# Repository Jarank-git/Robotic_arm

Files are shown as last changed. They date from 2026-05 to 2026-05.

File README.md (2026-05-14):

# Robotic Arm: Record/Playback & Hand Control

A robotic arm with four axes that is programmed using the Arduino Nano board and a shield. It offers four modes of control, namely, direct control using potentiometers, recording and playing back positions, and hand gestures using computer vision, all available and switchable over serial communication in real time.



## How It Works

The robotic arm consists of four joints that are powered by MG90S and SG90 servo motors. Four potentiometers are used as the main source of input control, with one for each joint. When turning a knob manually, it rotates its associated joint in real time. The Arduino Nano scans each potentiometer, converts the value to a corresponding pulse width in microseconds for the servo motor, and sends commands to the four servos in a timely manner. In addition to direct control, there are three other modes available, such as record, play, and gesture, all of which can be switched through serial communication.

| Command | Mode | Description |
|---|---|---|
| `0` | Normal | Potentiometers control servos in real time |
| `1` | Record | Position the arm and send `r` to save each step (up to 100) |
| `2` | Playback | Smooth looping replay of recorded steps |
| `3` | Gesture | Python takes over servo control via webcam |
| `h` | Help | Prints command menu to serial monitor |

## Firmware

Smooth motion of the arm without jitters involved many factors, among them averaging of multiple sensor values, careful handling of microseconds of signal for each joint's servos.

Averaging. The readings of each potentiometer are averaged after 30 sequential readings, 100µs apart from each other. Otherwise, consecutive readings of analog signals will be affected by noise caused by capacitive effects, which manifest themselves in a permanent jittery behavior of the servos. Averaging the results over 30 times eliminates such artifacts.

Microsecond control. The servos are controlled not by write(), but by writeMicroseconds(). The former only offers 0-180 positions with an integer number between them. Using writeMicroseconds() allows for controlling the servo in a wide range of about 600-2400µs which is enough for smooth interpolation.

Timed polling loop. Reading the sensors as quickly as possible would produce jittery behavior as well as out-of-synchronicity of the joints. The firmware does its work at a predefined frequency of 25ms. Four potentiometers are read and all four servos' positions are updated in one sequence of actions: readPot(), mapping(), then move_servo(). Thus, the joints are always synchronized.

Array-based design. The values of ADC measurements of potentiometers are stored in sensVal[4]. Then, each of these numbers is converted to microseconds with map() function and stored in ist[4]. Then, move_servo() uses the numbers in this array to control the servo positions. In record mode, current ist[] array is copied to four different arrays named joint0-joint3 of 100 elements length.

Potentiometer calibration. The map() function is applied to convert sensVal[i] to ist[i] by calling map(sensVal[i], 0, 650, 600, 2400). This map uses 650 as an upper limit while 1023 is the actual maximum value. After measuring the actual rotation angle of the potentiometer, I found that only a limited rotation gives max ADC value. Therefore, the maximum value for potentiometer rotation was actually 650, and using it as the upper boundary allows for recording a full rotation without any problems.

Ease-in-out playback. When playing back the recorded data, the transitions are not abrupt. A smooth movement of the arm happens due to interpolation and cosine easing algorithm which splits each transition into 50 steps, making the whole transition take about 800ms. The cosine function generates a natural movement pattern, starting slow as the joint accelerates, reaching peak speed through the middle, then decelerating to a stop at the target position.

## Gesture Control

The gesture control script uses MediaPipe Hands to track a hand through a webcam feed and maps the number of extended fingers to servo axes on the arm. MediaPipe returns 21 landmarks per hand, one for each joint and fingertip. To determine whether a finger is extended, the script compares the y-coordinate of the fingertip landmark to the y-coordinate of the knuckle two joints down. Since y increases downward in image coordinates, a fingertip with a lower y value than its knuckle means the finger is pointing up and therefore extended.

The finger count maps directly to which servo moves: 1 finger drives servo 1, 2 fingers servo 2, and so on. Each servo has a direction variable that starts positive, incrementing the position by a fixed step each frame. When the position hits the 2400µs ceiling or 600µs floor, the direction flips and the servo starts moving back. This gives continuous bouncing motion as long as fingers are held up, which makes it intuitive to control. The number of fingers held up determines which joint is active.

The script connects to the Nano on COM3 at 9600 baud, sends a 3 to switch it into gesture mode, and then streams S s1 s2 s3 s4 commands every frame. The Nano parses each incoming S command and writes the four values directly to the servos.

Dependencies: pyserial, opencv-python, mediapipe

## Assembly

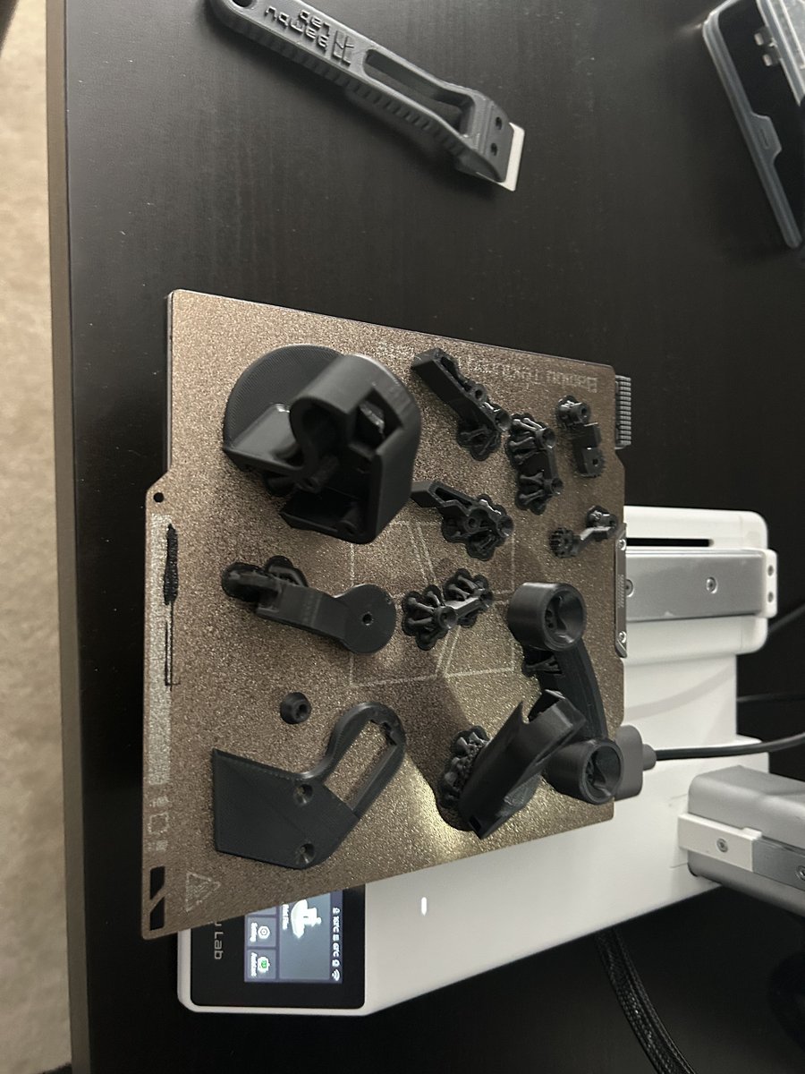
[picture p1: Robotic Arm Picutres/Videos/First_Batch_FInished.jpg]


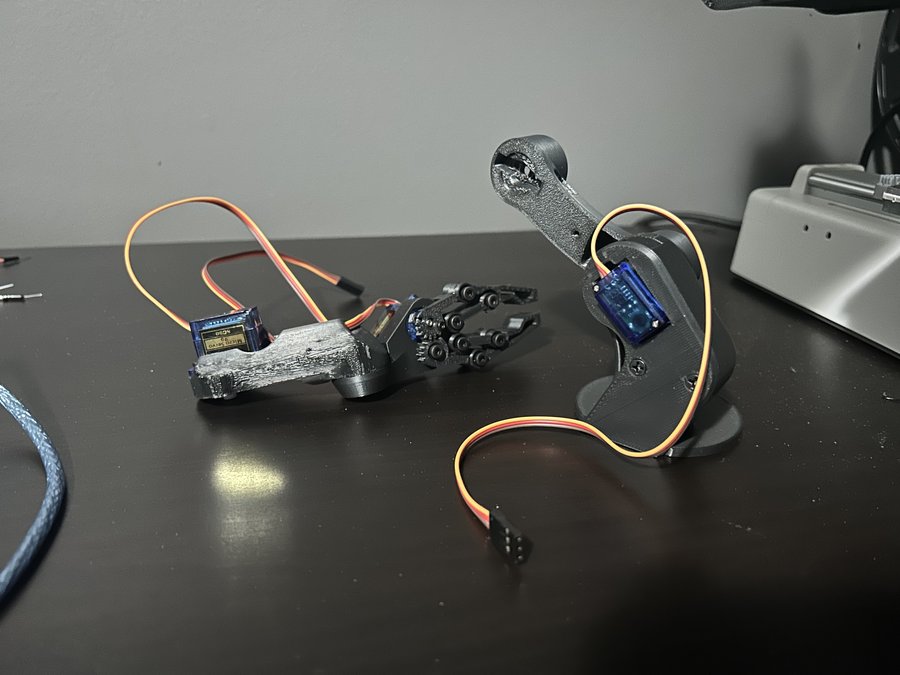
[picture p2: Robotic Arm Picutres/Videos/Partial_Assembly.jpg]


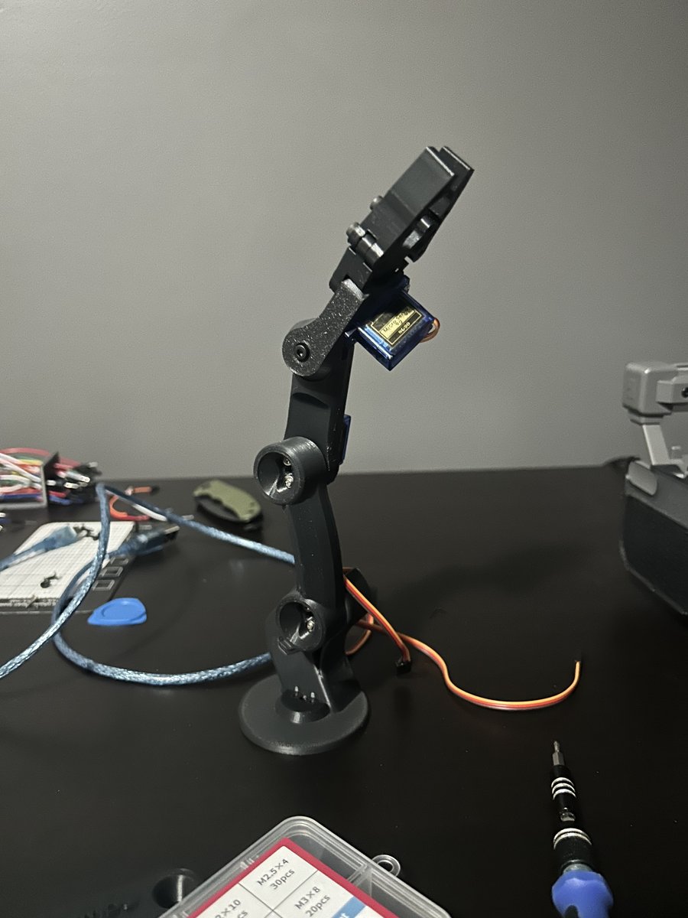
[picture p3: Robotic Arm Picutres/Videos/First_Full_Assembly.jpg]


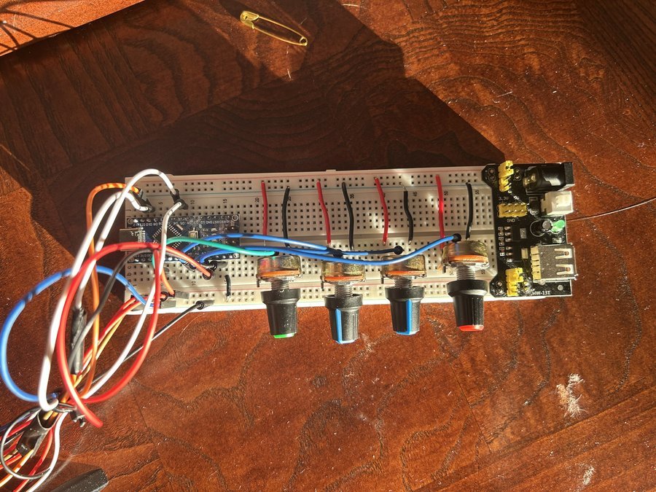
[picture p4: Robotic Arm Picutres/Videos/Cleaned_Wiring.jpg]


All the parts were made using PLA through 3D printing. However, there were a few modifications made before the parts were finalized. Initially, the prints came out perfect, and assembly progressed well until it was time to test the claw. The first problem was with the claw. The screw hole position in the original part file was inaccurate, resulting in improper interaction between the gears attached to the fingers of the claw. This led to a situation where only one claw out of the two was correctly closing, the other was not recieving power through the gears. To correct this problem, I uploaded the part file to Autodesk Fusion and then measured the distance from the screw hole to its required position based on the gear geometry. This information was used to relocate the hole, and then it was reprinted successfully, and the mechanism worked in the desired way. The next problem encountered was with the connector arm. The connector arm is a component that connects the claw to the main arm through a channel meant for an M3 nut that screws into the claw mechanism. The channel was small and not able to hold the nut. This problem was corrected by opening up the channel in Autodesk Fusion and then reprinting the part successfully. Both modified STEP files are in the CAD folder with full credit to the original designer.

## PCB & Schematics

The first prototype of the build made use of a breadboard to link up the Nano, potentiometers, and servo signal lines. It did work, although it was untidy and prone to failure; wires would move out of place and connections would come loose when the robot moved. In order to make things cleaner and more efficient, I came up with a design for my own PCB shield, done using Altium Designer. This allows all the components to fit onto one PCB, which is placed on top of the Nano. The Altium source files are included in the PCB + Schematic folder.

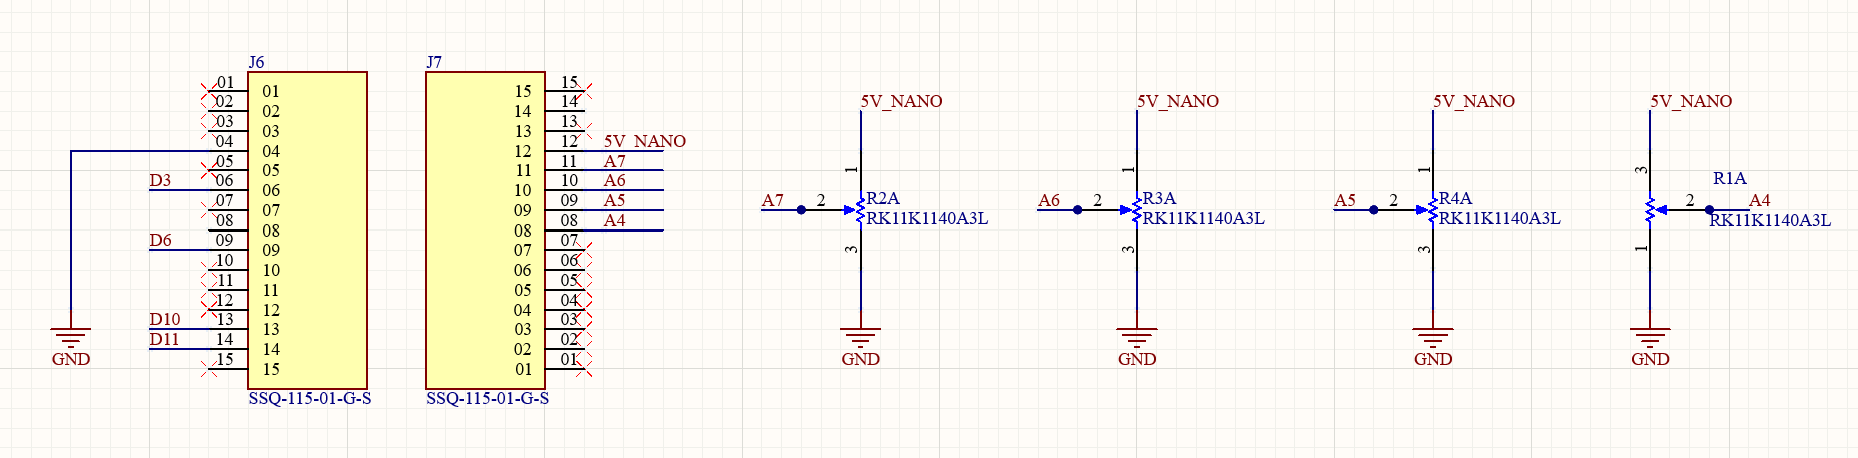
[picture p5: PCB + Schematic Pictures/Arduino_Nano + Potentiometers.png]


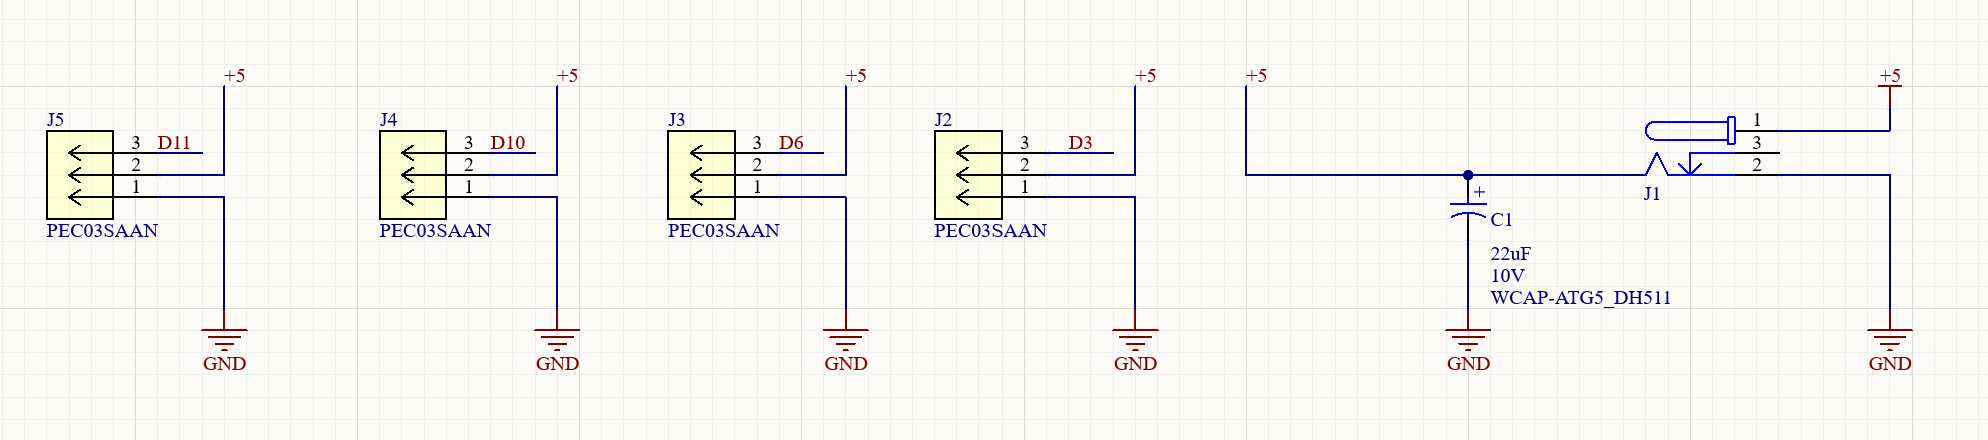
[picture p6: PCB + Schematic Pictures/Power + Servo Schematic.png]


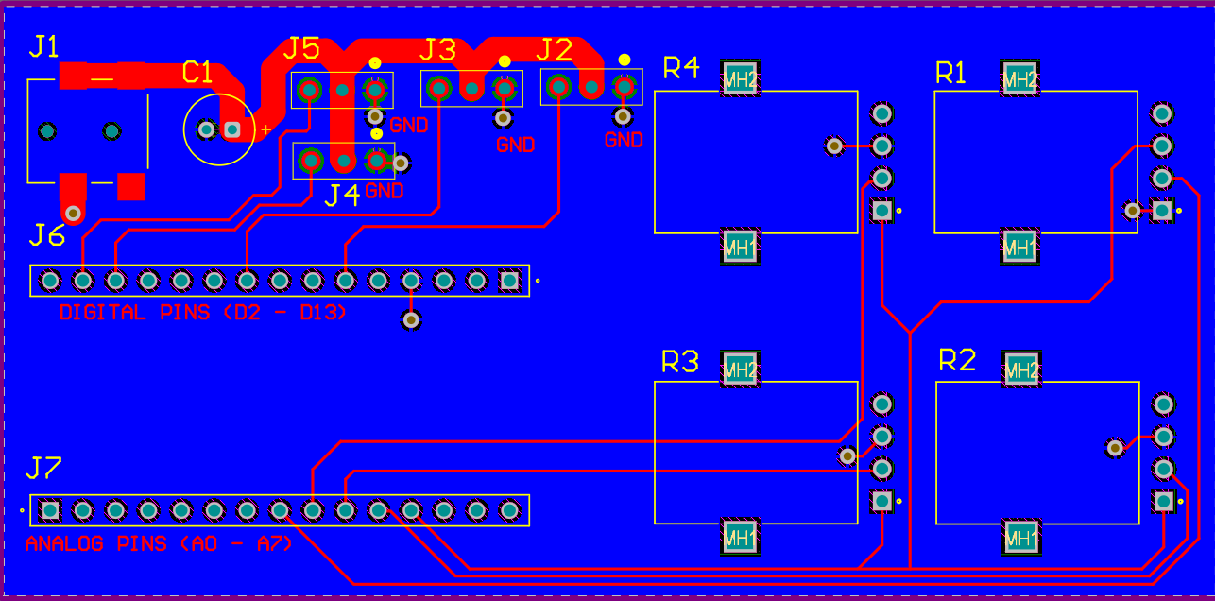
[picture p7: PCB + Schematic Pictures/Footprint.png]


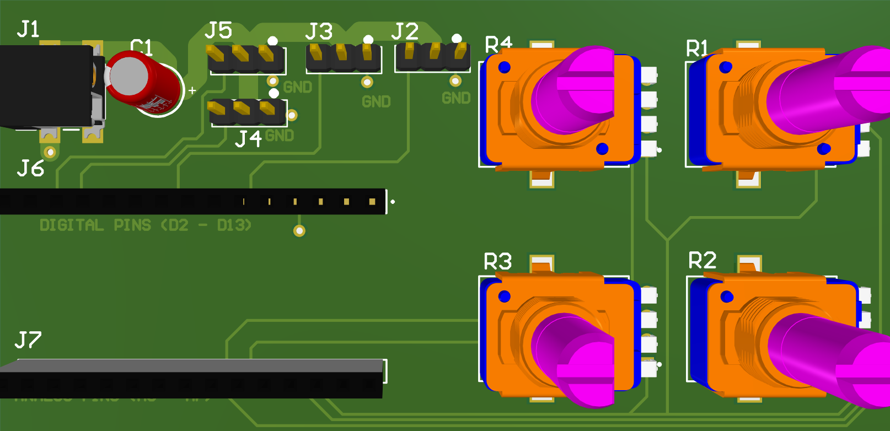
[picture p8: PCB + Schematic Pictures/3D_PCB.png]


## Hardware

| Component | Details |
|---|---|
| Microcontroller | Arduino Nano (ATmega328P) |
| Servos | 4× MG90S / SG90 |
| Potentiometers | 4× 10kΩ |
| Wiring | Jumper wires |
| PCB | Custom shield designed in Altium Designer |
| 3D Printed Parts | PLA |
| Framework | PlatformIO |

## Demo Videos

- Gesture Control: https://youtu.be/HV5-AcP3Ts8
- Record / Playback: https://youtu.be/INzKYXssj1g
- Manual Control: https://youtu.be/m88PAH4PIvc

## Build & Flash

Requires [PlatformIO](https://platformio.org/). With the Nano on COM3:

```bash
pio run --target upload
pio device monitor --baud 9600
```

Send h in the serial monitor for the full command reference.

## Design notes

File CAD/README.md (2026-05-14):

# CAD Files

## Credits

The original robotic arm models were designed by **FABRI CREATOR** — all credit for the base design goes to them.

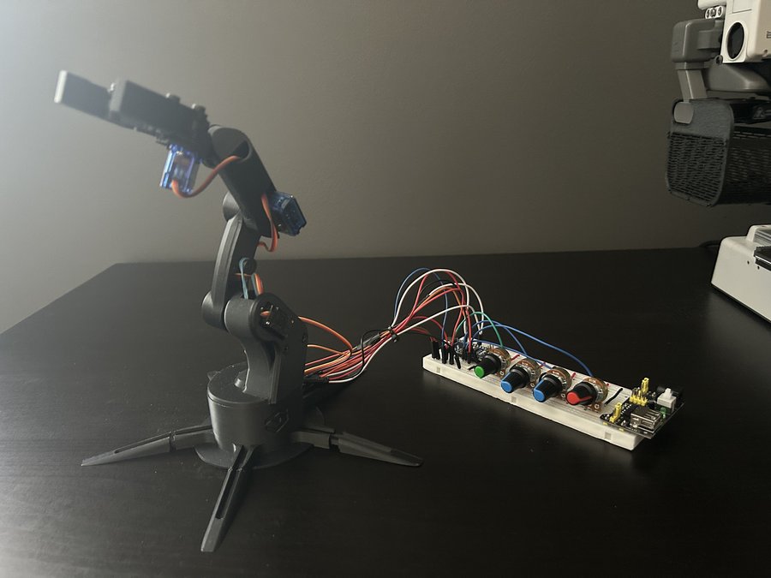
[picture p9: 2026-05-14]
Robotic Arm Picutres/Videos/Final_Product.jpg

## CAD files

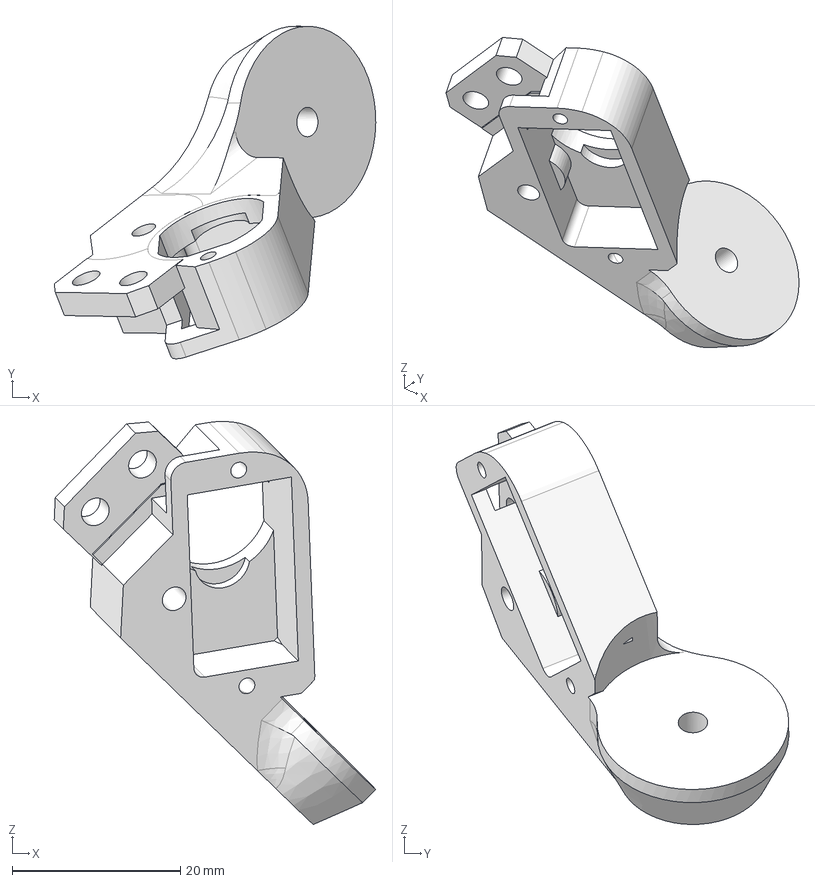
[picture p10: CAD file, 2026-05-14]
CAD/Modified+Claw+Arm.stp
38.3 x 39.6 x 48.0 mm
SG90 - Micro Servo 9g - Tower Pro v2
SG90 - Micro Servo 9g - Tower Pro.3 (1) x 2
SG90 - Micro Servo 9g - Tower Pro.5 (1) x 4
SG90 - Micro Servo 9g - Tower Pro.6 (1) x 2
Engranaje1
Engranaje2
Barra2
Garra1
Barra1
Garra2
Eje Garra2 (1)
Base de la Garra x 2
SG90 - Micro Servo 9g - Tower Pro.1 (1)
Servo sg90 (1)
Antebrazo
Brazo
Base (2) x 2
Eje Central (1)
Potentiometer (1)
Engranaje1 (1)
Engranaje2 (1)
Garra1 (1)
Barra2 (1)
Barra1 (1)
Garra2 (1)
Base de la Garra (1)
SG90 SERVOMOTOR x 3
Potentiometer (1) v1 (5)
Potentiometer (1) v1 (6)
Potentiometer (1) v1 (7)
Potentiometer (1) v1 (8)
Antebrazo (1)
Brazo (1)
Base (2) (1) x 2
Tapa Eje
Tubito
Eje Central (1) (1)
perilla v12
perilla v12 (1)
perilla v12 (2)
perilla v12 (3)
Base del brazo y circuito
Pata (1)
Pata (4)
Pata (3)
Pata (2)
Tapa para potenciometros solos(1)
Caja de solo potenciómetros(1)
Pata(5)

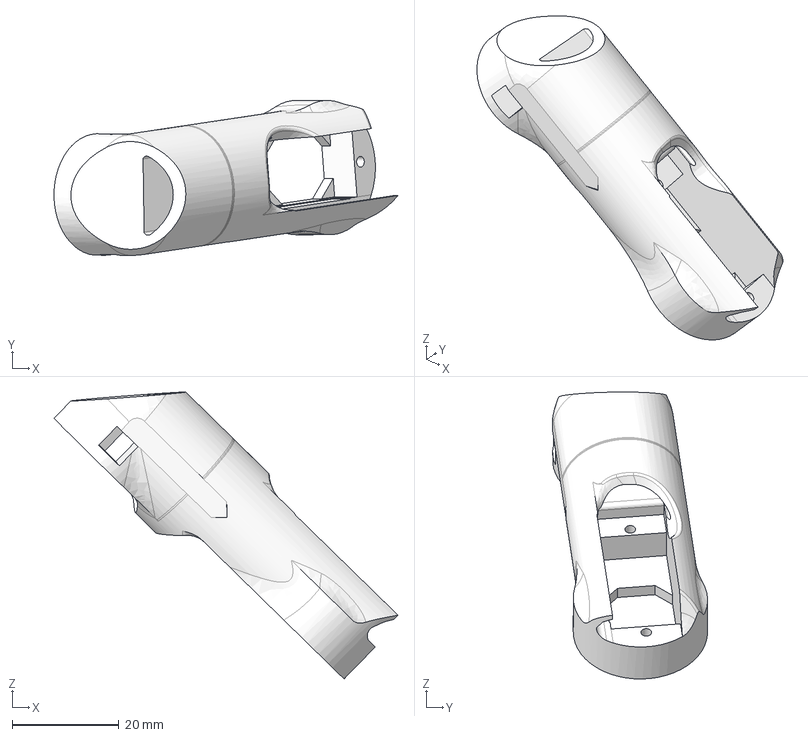
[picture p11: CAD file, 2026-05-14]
CAD/Modified+Connector+Arm.stp
64.5 x 29.1 x 53.8 mm
SG90 - Micro Servo 9g - Tower Pro v2
SG90 - Micro Servo 9g - Tower Pro.3 (1) x 2
SG90 - Micro Servo 9g - Tower Pro.5 (1) x 4
SG90 - Micro Servo 9g - Tower Pro.6 (1) x 2
Engranaje1
Engranaje2
Barra2
Garra1
Barra1
Garra2
Eje Garra2 (1)
Base de la Garra x 2
SG90 - Micro Servo 9g - Tower Pro.1 (1)
Servo sg90 (1)
Antebrazo
Brazo
Base (2) x 2
Eje Central (1)
Potentiometer (1)
Engranaje1 (1)
Engranaje2 (1)
Garra1 (1)
Barra2 (1)
Barra1 (1)
Garra2 (1)
Base de la Garra (1)
SG90 SERVOMOTOR x 3
Potentiometer (1) v1 (5)
Potentiometer (1) v1 (6)
Potentiometer (1) v1 (7)
Potentiometer (1) v1 (8)
Antebrazo (1)
Brazo (1)
Base (2) (1) x 2
Tapa Eje
Tubito
Eje Central (1) (1)
perilla v12
perilla v12 (1)
perilla v12 (2)
perilla v12 (3)
Base del brazo y circuito
Pata (1)
Pata (4)
Pata (3)
Pata (2)
Tapa para potenciometros solos(1)
Caja de solo potenciómetros(1)
Pata(5)

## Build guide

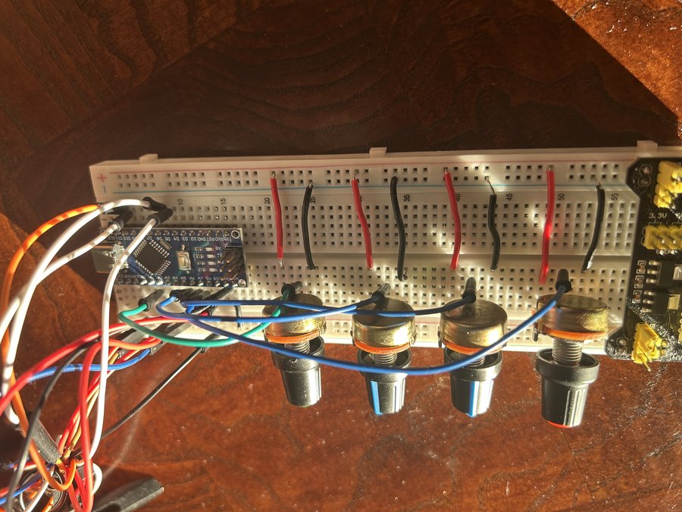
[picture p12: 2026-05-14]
Robotic Arm Picutres/Videos/Wiring.jpg

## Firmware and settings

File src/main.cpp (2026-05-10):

#include <Arduino.h>
#include <Servo.h>

Servo servo1;
Servo servo2;
Servo servo3;
Servo servo4;
int joint0[100];
int joint1[100];
int joint2[100];
int joint3[100];
int mode(0);
int stepCount(0);
int currentStep(0);
int sensVal[4];
float ist[4];
unsigned long previous_time(0);
unsigned long lastRecord(0);
int lastMode(-1);
const int stepDuration = 800; // ms per step transition during playback

// ease-in-out curve slow start, fast middle, slow end for natural motion, using a fcn (cos) to model the behaviour
float easeInOut(float t) {
    return -(cos(PI * t) - 1.0f) / 2.0f;
}

//fcn to smoothly move servos from one recorded position to the next over duration_ms
void smoothMove(int f0, int t0, int f1, int t1, int f2, int t2, int f3, int t3, int duration_ms) {
    const int steps = 50;
    int stepDelay = duration_ms / steps;
    for (int i = 0; i <= steps; i++) {
        //check for mode change midmove so user can interrupt
        if (Serial.available() > 0) break;
        float ease = easeInOut((float)i / steps);
        servo1.writeMicroseconds(f0 + ease * (t0 - f0));
        servo2.writeMicroseconds(f1 + ease * (t1 - f1));
        servo3.writeMicroseconds(f2 + ease * (t2 - f2));
        servo4.writeMicroseconds(f3 + ease * (t3 - f3));
        delay(stepDelay);
    }
}

//function to average the analogRead from each potentiometer to reduce noise, thus reducing jittering
unsigned int averageFcn(int pin) {
    unsigned int count(0);
    for(unsigned int i(0); i < 30; i++){
        count += analogRead(pin);
        delayMicroseconds(100);
    }
    count /= 30;
    return count;
}

void readPot() {
    sensVal[0] = averageFcn(A7);
    sensVal[1] = averageFcn(A6);
    sensVal[2] = averageFcn(A5);
    sensVal[3] = averageFcn(A1);
}


//mapping the manual potentiometer values, 0 - 650 calibrated for my setup, to 600 - 2400 for microsecond movements
void mapping() {
    ist[0] = map(sensVal[0], 0, 650, 600, 2400);
    ist[1] = map(sensVal[1], 0, 650, 600, 2400);
    ist[2] = map(sensVal[2], 0, 650, 600, 2400);
    ist[3] = map(sensVal[3], 0, 650, 600, 2400);
}

//function to merge all servo movements into 1 fcn
void move_servo() {
    servo1.writeMicroseconds(ist[0]);
    servo2.writeMicroseconds(ist[1]);
    servo3.writeMicroseconds(ist[2]);
    servo4.writeMicroseconds(ist[3]);
}

// fcn that handles recording each servo motor's movement to the respective array
void recordStep() {
    if (stepCount < 100) {
        // use the ist[] values already updated by the loop — no need to re-read pots
        joint0[stepCount] = ist[0];
        joint1[stepCount] = ist[1];
        joint2[stepCount] = ist[2];
        joint3[stepCount] = ist[3];
        stepCount++;

        Serial.print("Step ");
        Serial.print(stepCount);
        Serial.println(" recorded. Send 'r' for next step, '2' to play back.");
    } else {
        Serial.println("Memory full (100 steps). Send '2' to play back.");
    }
}

// fcn to handle the playback of the values stored in the array from the recordStep fcn
void playBack() {
    if (stepCount == 0) {
        Serial.println("No steps recorded. Record some first (send '1', then 'r').");
        mode = 0;
        return;
    }

    //on first step, snap directly to starting position then begin smooth transitions
    if (currentStep == 0) {
        servo1.writeMicroseconds(joint0[0]);
        servo2.writeMicroseconds(joint1[0]);
        servo3.writeMicroseconds(joint2[0]);
        servo4.writeMicroseconds(joint3[0]);
        currentStep = 1;
        return;
    }

    Serial.print("Playing step ");
    Serial.print(currentStep + 1);
    Serial.print(" / ");
    Serial.println(stepCount);

    smoothMove(
        joint0[currentStep - 1], joint0[currentStep],
        joint1[currentStep - 1], joint1[currentStep],
        joint2[currentStep - 1], joint2[currentStep],
        joint3[currentStep - 1], joint3[currentStep],
        stepDuration
    );

    currentStep++;
    if (currentStep >= stepCount) {
        currentStep = 0;
        Serial.println("Loop complete. Repeating... Send '0' to stop.");
    }
}

//prints the command menu to the serial monitor
void printHelp() {
    Serial.println("--- Commands ---");
    Serial.println("  0  : Normal mode (potentiometer control)");
    Serial.println("  1  : Record mode (position arm, send 'r' to save each step)");
    Serial.println("  2  : Playback mode (smooth replay of recorded steps)");
    Serial.println("  3  : Gesture mode (python controls servos)");
    Serial.println("  r  : Record current position (record mode only)");
    Serial.println("  h  : Show this help");
    Serial.println("----------------");
}


//reads and processes all incoming serial commands (mode switches, record trigger, gesture S commands)
void handleButtons() {
    while (Serial.available() > 0) {
        char cmd = Serial.read();
        if (cmd == '\r' || cmd == '\n') continue;

        if (cmd == '0') { mode = 0; }
        else if (cmd == '1') { mode = 1; stepCount = 0; }
        else if (cmd == '2') { mode = 2; currentStep = 0; }
        else if (cmd == '3') { mode = 3; }
        else if (cmd == 'S') {
            char buf[24];
            int len = Serial.readBytesUntil('\n', buf, sizeof(buf) - 1);
            if (mode == 3) {
                buf[len] = '\0';
                int s1, s2, s3, s4;
                if (sscanf(buf, "%d %d %d %d", &s1, &s2, &s3, &s4) == 4) {
                    servo1.writeMicroseconds(s1);
                    servo2.writeMicroseconds(s2);
                    servo3.writeMicroseconds(s3);
                    servo4.writeMicroseconds(s4);
                }
            }
        }
        else if (cmd == 'r' && mode == 1 && millis() - lastRecord > 300) {
            readPot();
            mapping();
            lastRecord = millis();
            recordStep();
        }
        else if (cmd == 'h') { printHelp(); }
    }
}

//when an option is selected accurately state the correct mode in the serial monitor
void printModeChange() {
    if (mode != lastMode) {
        lastMode = mode;
        if (mode == 0) Serial.println("[MODE] Normal — move arm with potentiometers.");
        if (mode == 1) Serial.println("[MODE] Record — position arm and send 'r' to save each step.");
        if (mode == 2) Serial.println("[MODE] Playback — smooth replay of recorded steps. Send '0' to stop.");
        if (mode == 3) Serial.println("[MODE] Gesture — python is controlling servos.");
    }
}


//attaching all servos based off of my circuit, can change on your wiring
void setup() {
    servo1.attach(5);
    servo2.attach(11);
    servo3.attach(10);
    servo4.attach(6);
    pinMode(13, OUTPUT);
    Serial.begin(9600);
    Serial.setTimeout(200);
    analogReference(DEFAULT);

    //smooth opening sequence
    readPot();
    mapping();
    move_servo();

    Serial.println("Send 'h' for help.");
    printHelp();
}

void loop() {
    handleButtons();
    printModeChange();
    unsigned long current_time(millis());

    // potentiometer polling runs in modes 0 and 1; mode 2 runs playback; mode 3 is handled entirely in handleButtons
    if (mode == 0 || mode == 1) {
        if (current_time - previous_time >= 25) {
            previous_time = current_time;
            readPot();
            mapping();
            move_servo();
        }
    }

    if (mode == 2) {
        playBack();
    }
}

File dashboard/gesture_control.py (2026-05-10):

import serial
import time
import cv2
import mediapipe as mp

port = "COM3"
baud = 9600

#neutral position for gesture control saved in array for each servo 1 - 4
positions = [1500, 1500, 1500,1500 ]
#keep track of directions 1 = rotating clockwise, -1 = rotating anti-clockwise
directions = [1, 1, 1, 1]
#how much to move each motor by, ensuring smooth movement
step = 20
min_Pos = 600
max_Pos = 2400

# let DTR reset happen naturally (same approach as the working version),
# then wait for Arduino to finish booting before sending anything
arm = serial.Serial(port, baud, timeout=1)
time.sleep(2)
arm.reset_input_buffer()
arm.write(b'3')
arm.flush()
time.sleep(0.3)
response = arm.read_all().decode('utf-8', errors='ignore')
if '[MODE] Gesture' in response:
    print("Gesture mode confirmed!")
else:
    print(f"WARNING: mode 3 not confirmed. Got: {response!r}")

#limit # of hands to 1, and setup video
mp_drawing = mp.solutions.drawing_utils
mp_hands = mp.solutions.hands
hands = mp_hands.Hands(max_num_hands=1)
cap = cv2.VideoCapture(0)

tip_ids = [4, 8, 12, 16, 20]

while True:
    ret,frame = cap.read()
    if not ret:
        break
    #reflect the camera
    frame = cv2.flip(frame, 1)
    #openCV gives bgr, mediapipe requires rgb convert
    rgb = cv2.cvtColor(frame, cv2.COLOR_BGR2RGB)
    #result of the analysis through mediapipeline
    result = hands.process(rgb)

    fingers_up = 0

    #check if a hand is visible then from there if it is create the landmarks
    if result.multi_hand_landmarks:
        #draw the 21 hand landmarks and skeleton connections onto the frame
        for hand_landmarks in result.multi_hand_landmarks:
            mp_drawing.draw_landmarks(frame, hand_landmarks, mp_hands.HAND_CONNECTIONS)
        landmarks = result.multi_hand_landmarks[0].landmark
        for i in range(1, 5):
            #fingertip y < knuckle y means the finger is extended (y increases downward in image coordinates)
            if landmarks[tip_ids[i]].y < landmarks[tip_ids[i] - 2].y:
                fingers_up +=1

        if fingers_up > 0:
            #fingers_up - 1 converts the count to a 0-based index (1 finger → servo 0, 2 → servo 1, etc.)
            idx = fingers_up - 1
            positions[idx] += step * directions[idx]


            if positions[idx] >= max_Pos or positions[idx] <= min_Pos:
                directions[idx] *= -1
            positions[idx] = max(min_Pos, min(max_Pos, positions[idx]))

    command = f"S {positions[0]} {positions[1]} {positions[2]} {positions[3]}\n"
    arm.write(command.encode())
    arm.flush()

    cv2.imshow("Gesture Control", frame)
    if cv2.waitKey(1) & 0xFF == ord('q'):
        break

cap.release()
cv2.destroyAllWindows()
arm.close()

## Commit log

2026-05-14 add PCB schematics, CAD files, and project assets
    [Arduino_Nano + Potentiometers.schDoc, Modified+Claw+Arm.stp, Modified+Connector+Arm.stp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]
2026-05-14 update README with build experience, assembly images, and project details
